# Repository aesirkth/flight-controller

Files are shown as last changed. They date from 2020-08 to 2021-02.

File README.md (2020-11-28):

# Flight Controller <!-- omit in toc -->

This is the embedded software on the Flight Controller for the project Mjollnir. The Flight Controller is on-board the rocket. The Flight Controller communicates with the ground through a radio link during all phases of the flight

The mission objectives for the Mjollnir project relevant to the electronics are the following:

**Primary objectives**

- **E.PO.1** Monitor the rocket while it is on the launchpad and give a “Go”/”No go” signal
- **E.PO.2** Control the rocket while it is on the launchpad
- **E.PO.3** Trigger the drogue parachute’s ejection after apogee
- **E.PO.4** Trigger the main parachute’s ejection before touchdown
- **E.PO.5** Support rocket recovery operations
- **E.PO.6** Record video footage from the rocket

**Secondary objectives**

- **E.SO.1** Send real-time telemetry from the rocket
- **E.SO.2** Receive & display real-time telemetry from the rocket at the Ground Station as long as the rocket is at a reasonable distance
- **E.SO.3** Send real-time video from the rocket
- **E.SO.4** Receive & display real-time video from the rocket at the Ground Station as long as the rocket is at a reasonable distance
- **E.SO.5** Acquire flight data with more sensors than those deemed “mission-critical”
- **E.SO.6** Store all flight data on-board the rocket for further analysis

All of them apply to some extent to the Flight Controller

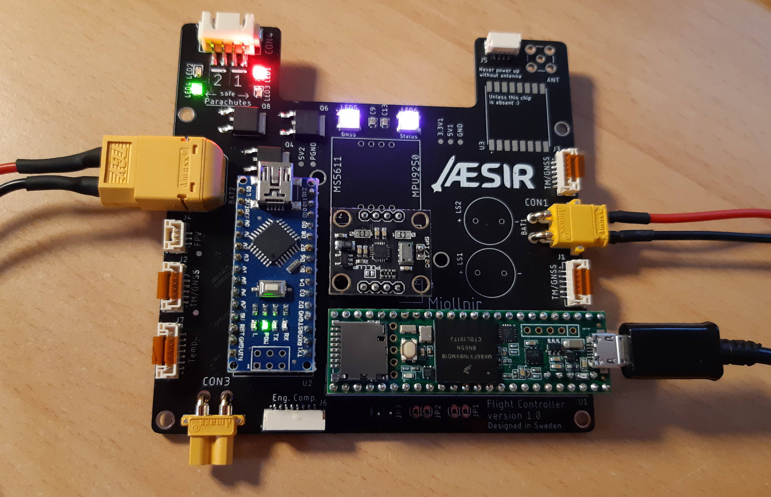
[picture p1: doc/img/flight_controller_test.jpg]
flight_controller_test


# Table of content <!-- omit in toc -->

- [Description](#description)
  - [Hardware](#hardware)
  - [Software](#software)
    - [Installation](#installation)
  - [Tests](#tests)
- [Data protocol](#data-protocol)
- [Folder structure](#folder-structure)

# Description

## Hardware

The Flight Controller is a single PCB with power management, sensors, radio communication, and driver for the actuators used during the flight.

It has the following features:

- Dual microcontroller (main + backup)
- Low power long range LoRa transceiver
- Telemetry output via serial link (x3)
- GNSS support via serial link (x3)
- Compatible with 10 dof breakout board with MS5611 pressure sensors and MPU9250 IMU (2x)
- Compatible with K type thermocouples (2x)
- Flash memory
- EEDs driver for parachute ejection, with ESD protection + visual and audible warning (2x)
- RGB leds to display the board status
- Serial link to FPV transmitter
- CAN Bus

A more detailed description of the hardware is given in [doc/hardware_description.md](doc/hardware_description.md)

## Software

This repository uses [PlatformIO](https://platformio.org/) as the development tool for the two microcontrollers on the Flight Controller.

### Installation

1. Install [PlatformIO Core](https://docs.platformio.org/en/latest/core/index.html) or [PlatformIO IDE](https://platformio.org/install/ide) on your computer
2. Clone this repository
3. [Linux] install [udev](https://docs.platformio.org/en/latest/faq.html?highlight=99#platformio-udev-rules) rules

## Tests

See [test/](test/)

# Data protocol

The protocol to communicate between the Ground Station and the Rocket is detailed in [doc/data_protocol](doc/data_protocol.md)

# Folder structure

```
.
├── doc/
│   ├── img/
│   ├── diagrams/
│   ├── sources
│   |   └── flight_controller_v1.0.pdf
│   ├── data_protocol.md
│   └── hardware_description.md
├── include/
│   ├── hardware_definition_nano.h
│   └── hardware_definition_teensy.h
├── src/                                    // Code folder
│   └── test_companion_teensy.cpp           // Use with hardware_test_teensy
├── test/                                   // Unit tests
│   ├── hardware_test_nano/
│   ├── hardware_test_teensy/
│   └── README.md                           // Documentation for the tests
├── env_nano.ini                            // Extra platformIO config
├── env_teensy.ini                          // Extra platformIO config
├── LICENSE
├── platformio.ini                          // PlatformIO config
└── README.md                               // This file
```

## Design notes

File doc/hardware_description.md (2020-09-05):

# Hardware description <!-- omit in toc -->

*This page describes the version 1.0 of the Flight Controller*

<p align="middle">
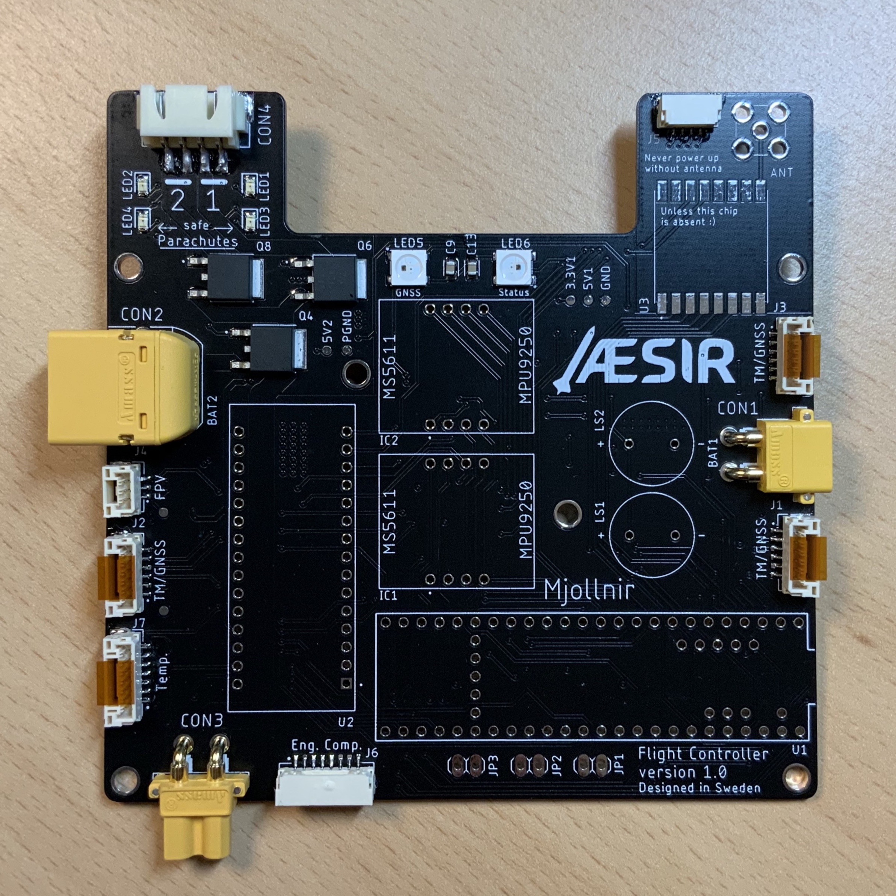
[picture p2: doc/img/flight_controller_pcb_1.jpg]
    
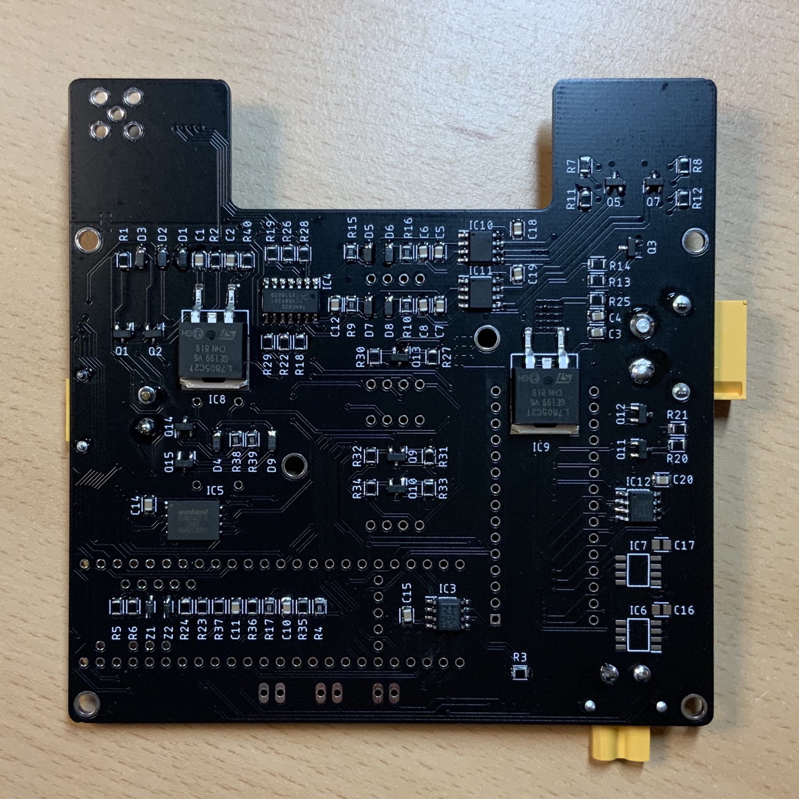
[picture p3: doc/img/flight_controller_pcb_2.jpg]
    
</p>

>Top side and bottom side of the Flight Controller PCB

The schematic of the Flight Controller is here [doc/sources/flight_controller_v1.0.pdf](sources/flight_controller_v1.0.pdf)<br>
The Eagle source files are also available as [doc/sources/flight_controller_v1.0.sch](doc/../sources/flight_controller_v1.0.sch) and [doc/sources/flight_controller_v1.0.brd](doc/../sources/flight_controller_v1.0.brd)

# Table of contents <!-- omit in toc -->

- [Purpose](#purpose)
- [Microcontrollers](#microcontrollers)
- [Power](#power)
  - [Input](#input)
  - [Output](#output)
  - [Turn on the board](#turn-on-the-board)
  - [Power from USB](#power-from-usb)
- [Parachute drivers](#parachute-drivers)
- [Sensors](#sensors)
  - [On the board](#on-the-board)
    - [Air pressure](#air-pressure)
    - [Acceleration & angular velocity](#acceleration--angular-velocity)
  - [Off the board](#off-the-board)
    - [Differential air pressure sensor](#differential-air-pressure-sensor)
    - [Temperature sensors](#temperature-sensors)
- [Radio communication](#radio-communication)
- [GNSS receiver](#gnss-receiver)
- [Flash memory](#flash-memory)
- [Visual and audible signals](#visual-and-audible-signals)
  - [RGB leds](#rgb-leds)
  - [Buzzer](#buzzer)
- [Connectors](#connectors)
  - [Signal](#signal)
    - [Pin numbering](#pin-numbering)
    - [[J1] TM/GNSS](#j1-tmgnss)
    - [[J2] TM/GNSS](#j2-tmgnss)
    - [[J3] TM/GNSS](#j3-tmgnss)
    - [[J4] FPV](#j4-fpv)
    - [[J5] Air pressure sensor](#j5-air-pressure-sensor)
    - [[J6] Engine Computer](#j6-engine-computer)
    - [[J7] External temperature](#j7-external-temperature)
    - [[JP1] Liftoff 1](#jp1-liftoff-1)
    - [[JP2] Liftoff 2](#jp2-liftoff-2)
    - [[JP3] Master Switch](#jp3-master-switch)
  - [Power](#power-1)
    - [[CON1] Battery 1 input](#con1-battery-1-input)
    - [[CON2] Battery 2 input](#con2-battery-2-input)
    - [[CON3] Engine Output](#con3-engine-output)
    - [[CON4] Parachute drivers](#con4-parachute-drivers)
  - [Antenna](#antenna)
    - [[ANT] LoRa antenna](#ant-lora-antenna)

# Purpose

- Validate the overall design of the Flight Controller
- Support the first static fire at the end of the summer 2020
- Support the first tests of the parachute system
- Support the beginning of the code development for the future flight hardware

# Microcontrollers

The Flight Controller has two microcontrollers

| Name | Device | Role | Power |
| --- | --- | --- | ----- |
| Main controller | Teensy 3.6 | Handle the flight data acquisition, parachute ejection, Engine Computer and radio links | BAT1  |
| Backup controller | Arduino Nano | Eject the parachutes in case the main controller fails | BAT2  |

# Power

## Input

Two separate battery inputs are available on the Flight Controller

| Name | Voltage | Role | Connector | Connector type |
| ---- | --- | --- | --- | --- |
| BAT1 | 7.2V | Power the sensors and low power chips | CON1 | XT30, male |
| BAT2 | 11.1V | Power the EEDs for the parachutes, the Engine actuators, and the high power chips | CON2 | XT60, male |

## Output

| Voltage | Role | Connector | Connector type | Current rating |
| --- | --- | --- | --- | --- |
| Same as BAT2 | Power to the Engine | CON3 | XT30, female | Up to 15A |

## Turn on the board

Both batteries are required to use all the fonctions of the Flight Controller

The Flight Controller is ON when the signal `MS_SWITCH` is not tied to `GND` (internal pull-up).
When `MS_SWITCH` is (strongly) pulled down, all the power rails on the board are turned OFF.
The power output on `CON3` is also turned OFF.

`MS_SWITCH` is available on the following connectors :

- J6
- JP3

## Power from USB

Both microcontrollers have an USB input. Caution is required when using power battery power and the USB connection.

**Teensy 3.6**

The Teensy 3.6 board allows to physically isolate the `VIN` rail and the `VUSB` rail by cutting their respective pads apart.

Make sure to isolate `VIN` from `VUSB` on any Teensy used on the Flight Controller to avoid conflicts between the external supply and the usb supply.

<p align="middle">
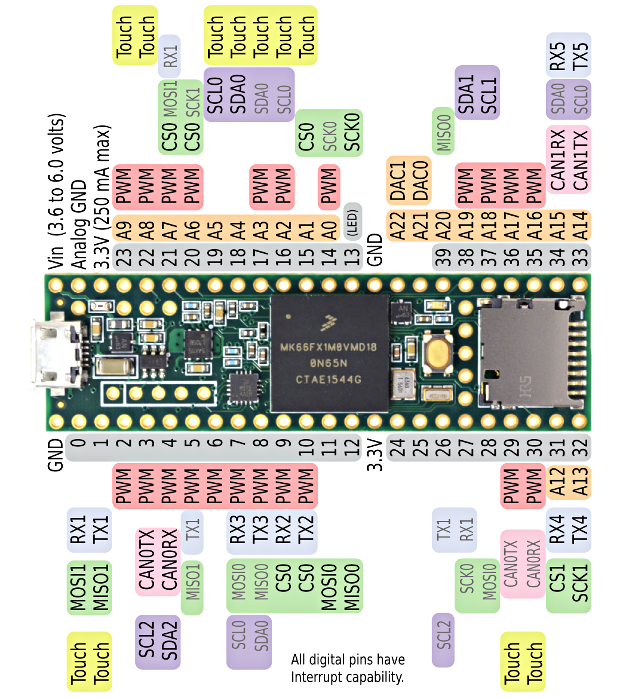
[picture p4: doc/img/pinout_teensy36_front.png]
    
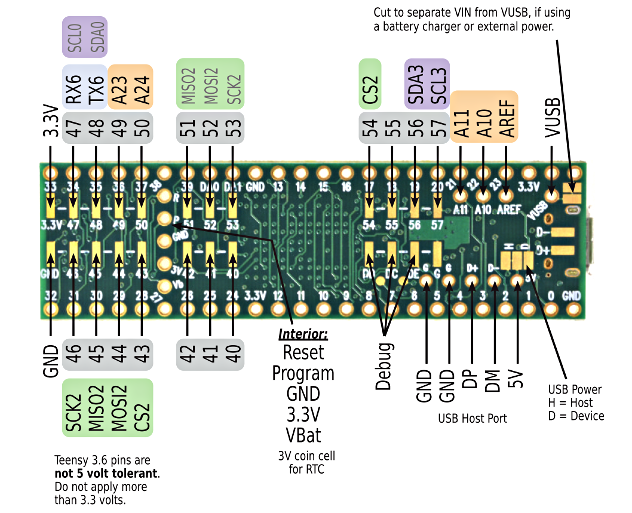
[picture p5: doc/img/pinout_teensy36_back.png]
    
</p>

**Arduino Nano**

The Nano board handles the power supply in a way that allows to use external power and USB power simultaneously. No modification is required.

# Parachute drivers

The Flight Controller can drive two independent parachutes at 12V/5A<br>
The parachutes are ejected from the rocket by Electro Explosive Devices

For safety reasons, both pins of the EEDs must be shorted and grounded when the parachutes are not energized.
This is done with an half H-bridge. The drivers' outputs are either shorted together and with the ground, or one of them is the ground and the other is connected to BAT2. Both the Teensy and the Arduino Nano can trigger the parachutes ejection. A signal from one of them is enough to energize the EED.

A led indicator next to the drivers connector `CON4` shows the state of the two outputs. The code on the Arduino and on the Teensy must activate their respective buzzers before any EED can be energized as a warning signal in case someone were to be close to the EED.

# Sensors

## On the board

### Air pressure

The static air pressure inside the rocket is measured with 2x **MS5611** sensors. The pressure inside the rocket must be equilibrated with the pressure outside the rocket.

A measure of the altitude is derivated from the static pressure

The **MS5611** chips are connected to the SPI bus 0 (`SPI`) of the Teensy.

### Acceleration & angular velocity

The acceleration and angular velocity of the rocket is measured with 2x **MPU9250** sensors. A 3-axis magnetometer is also available on the **MPU9250**.

The measurements from the **MPU9250** are meant to help derive an altitude value and to get the rocket attitude. The performance of the engine can also be recontructed from the acceleration curve during the propulsive phase.

The **MPU9250** are connected to the SPI bus 0 (`SPI`) of the Teensy

## Off the board

### Differential air pressure sensor

Located in the nosecone. ABPDRRT005PG2A5. Used to derive the Mach number

Connected to the I²C bus 0 (`SDA0` & `SCL0`). 5V logic, with level shifter

### Temperature sensors

The board features 2x **MAX31855K** thermocouple-to-digital converters to read the temperature from type_K thermocouples.

The thermocouples will be placed outside the rocket to measure the total air temperature.

The value of the external temperature will be used to derive the air speed during the flight, along with the Mach number

The **MAX31855K** are connected to the SPI bus 0 (`SPI`) of the Teensy

# Radio communication

An **RFM96W** LoRa transceiver at 433 MHz is mounted on the PCB and must always be connected to a 50Ω antenna. It is used as a low power device to receive TC and send the rocket position at low datarates during the flight and after landing.

The **RFM96W** is connected to the SPI bus 1 (`SPI1`) of the Teensy

An **RFD900+** (868MHz) modem can be connected on the **TM/GNSS** connectors of the board

The **RFD900+** is connected on the serial bus corresponding to the number of the connector it is connected to (`Serial1` for J1, `Serial2` for J2, `Serial3` for J3)

# GNSS receiver

A **NEO-M9N** GNSS receiver is used to acquire the rocket position during flight and after landing

The **NEO-M9N** can be used with one of the Serial buses available or over I²C

# Flash memory

A **W25N01GV** flash memory chip (1 Gbit) is available on the Flight Controller to log the flight data

It is connected to the SPI bus 1 (`SPI1`) of the Teensy

# Visual and audible signals

## RGB leds

Two **SK6812** RGB leds are used to display the status of the GNSS signal and the state of the Teensy. The leds are wired in series and are controlled via pin `6` of the Teensy

## Buzzer

The Flight Controller features two CEM-1206S buzzers. One is drived by pin `2` of the Teensy, the other is drived by pin `10` of the Arduino Nano. They work at 2400 Hz.

# Connectors

<p align="middle">
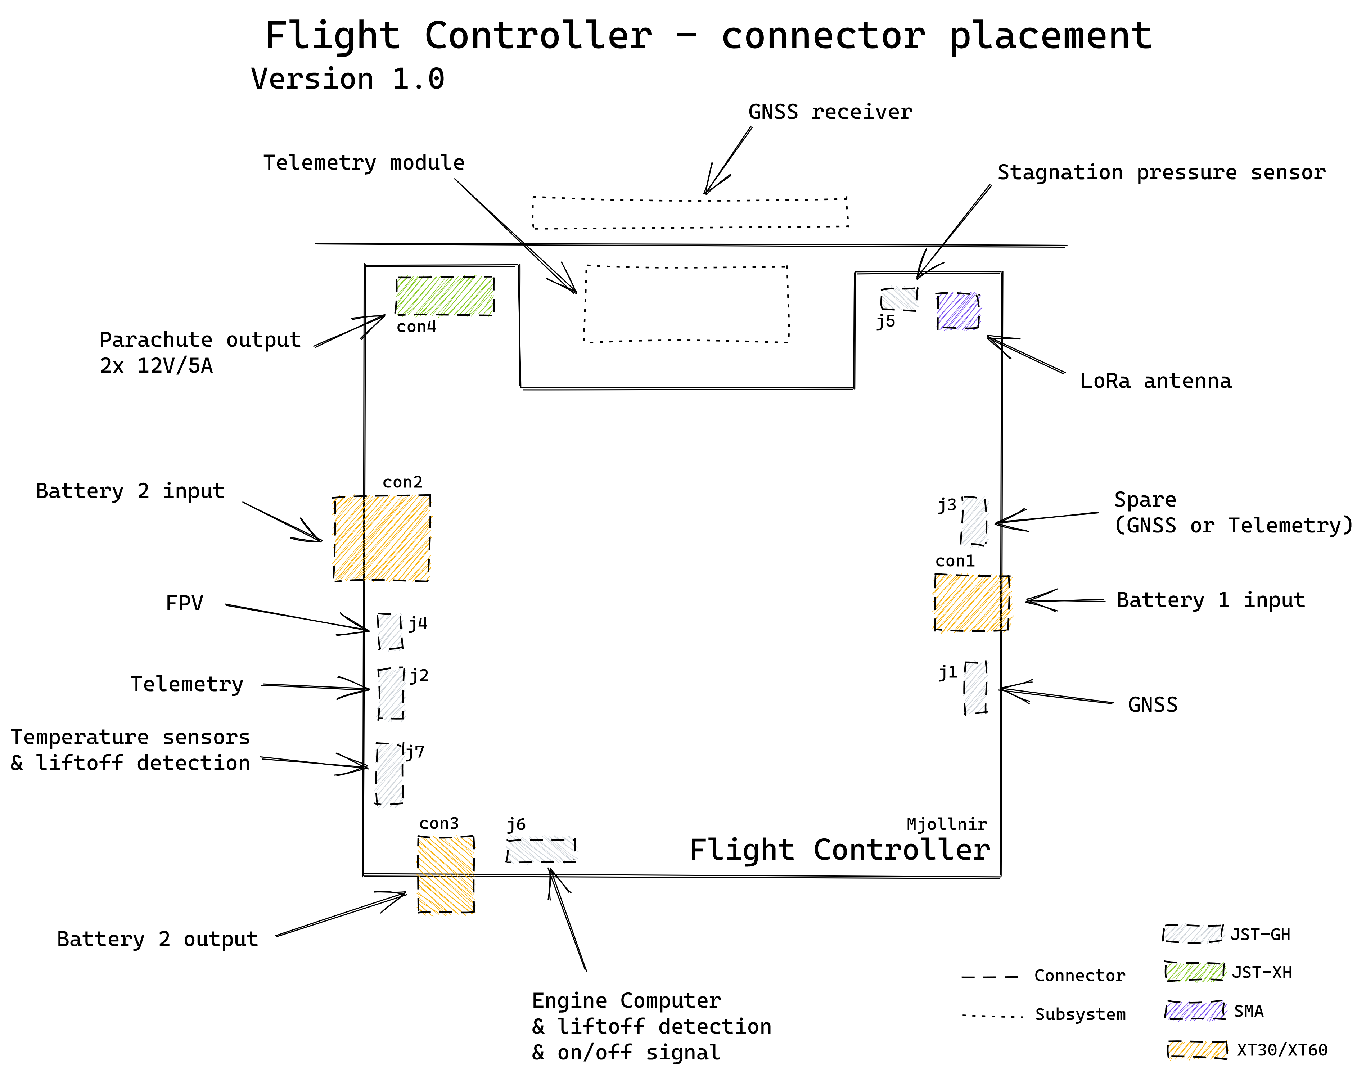
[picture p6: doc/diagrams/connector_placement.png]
    
</p>

## Signal

### Pin numbering

On all JST-GH connectors, pin 1 is the pin with the small triangle marking on the housing. It is also the pin closest to the small dot on the PCB silkscreen.

On all JST-XH connectors, pin 1 is the pin with the small rectangle or triangle marking on the housing.

### [J1] TM/GNSS

JST-GH, 6 pins

Connect a telemetry modem (low power) or a GNSS receiver

| Pin number | 1 | 2 | 3 | 4 | 5 | 6 |
| --- | --- | --- | --- | ---- | ---- | --- |
| Function | 5V1 | RX1 | TX1 | SCL0 | SDA0 | GND |

3.3V logic

### [J2] TM/GNSS

JST-GH, 6 pins

Connect a telemetry modem (high power, up to 1A) or a GNSS receiver<br>
The power on this pin can be turned ON (OFF) by setting pin `35` of the Teensy LOW (HIGH)

| Pin number | 1 | 2 | 3 | 4 | 5 | 6 |
| --- | --- | --- | --- | ---- | ---- | --- |
| Function | 5V2 | RX2 | TX2 | SCL0 | SDA0 | GND |

3.3V logic

### [J3] TM/GNSS

JST-GH, 6 pins

Connect a telemetry modem (low power) or a GNSS receiver

| Pin number | 1 | 2 | 3 | 4 | 5 | 6 |
| --- | --- | --- | --- | ---- | ---- | --- |
| Function | 5V1 | RX3 | TX3 | SCL0 | SDA0 | GND |

3.3V logic

### [J4] FPV

JST-GH, 3 pins

Connect an FPV module (camera + transmitter)<br>
The power on the pin can be turned ON (OFF) by setting pin `36` of the Teensy LOW (HIGH)

| Pin number | 1 | 2 | 3 |
| --- | ---- | --- | --- |
| Function | BAT2 | TX4 | GND |

3.3V logic

### [J5] Air pressure sensor

JST-GH, 4 pins

Connect a differential pressure sensor

| Pin number | 1 | 2 | 3 | 4 |
| --- | --- | ---- | ---- | --- |
| Function | 5V1 | SCL0 | SDA0 | GND |

5V logic

### [J6] Engine Computer

JST-GH, 8 pins

Connector to the Engine Computer<br>
Can provide 200 mA<br>
Also contains `MS_SWITCH` and `LIFTOFF_2` signals to the bottom of the rocket

| Pin number | 1 | 2 | 3 | 4 | 5 | 6 | 7 | 8 |
| --- | --- | --- | ----- | ----- | --- | --- | --- | --- |
| Function | 5V1 | GND | CANH0 | CANL0 | MS_SWITCH | GND | LIFTOFF_2 | GND |

3.3V logic

### [J7] External temperature

JST-GH, 7 pins

Two type-K thermocouples and `LIFTOFF_1` signal

| Pin number | 1 | 2 | 3 | 4 | 5 | 6 | 7 |
| --- | --- | --- | --- | --- | --- | --- | --- |
| Function | NC  | T1- | T1+ | T2- | T2+ | LIFTOFF_1 | GND |

3.3V logic

### [JP1] Liftoff 1

2.54 mm male pin header

Easy access to the `LIFTOFF_1` signal

| Pin | left | right |
| --- | --- | ----- |
| Function | LIFTOFF_1 | GND |

### [JP2] Liftoff 2

2.54 mm male pin header

Easy access to the `LIFTOFF_2` signal

| Pin | left | right |
| --- | --- | ----- |
| Function | LIFTOFF_2 | GND |

### [JP3] Master Switch

2.54 mm male pin header

Easy access to the `MS_SWITCH` signal

| Pin | left | right |
| --- | --- | ----- |
| Function | MS_SWITCH | GND |

## Power

### [CON1] Battery 1 input

XT-30, male

2S LiPo battery

### [CON2] Battery 2 input

XT-60, male

3S LiPo battery

### [CON3] Engine Output

XT-30, female

Power output to the Engine actuators<br>
From BAT2, max 15A

### [CON4] Parachute drivers

JST-XH, 4 pins

Outputs to the parachutes' EEDs<br>
Rated 12V/3A, can deliver 5A for short periods

| Pin number | 1 | 2 | 3 | 4 |
| --- | --- | --- | --- | --- |
| Function | GND | PARACHUTE_1 | GND | PARACHUTE_1 |

## Antenna

### [ANT] LoRa antenna

50Ω SMA connector

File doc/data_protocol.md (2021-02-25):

# Data Protocol <!-- omit in toc -->

Here is a description of the data protocol between the Rocket and the Ground Station for the Mjollnir project.

This protocol defines how Telecommands and Telemetry are transmitted between the Ground Station, the Engine Computer, and the Flight Controller.

The following repositories follow this data protocol:

- [aesirkth/flight-controller](https://github.com/aesirkth/flight-controller)
- [aesirkth/ground-control](https://github.com/aesirkth/ground-control)
- *engine computer repository*

The diagrams in this document can be edited using the online tool [diagrams.net](https://www.diagrams.net/). Just import the `.xml` files. Export the diagrams to `.png` and to `.xml` (compressed) and save them back here after modification.

The HTML tables in this document can be edited using the online tool [tablesgenerator.com](https://www.tablesgenerator.com/html_tables). Simply click "File / Paste table data" and paste the table. Make sure to check "Do not generate CSS" and uncheck "Compact mode".

# Table of contents <!-- omit in toc -->

- [Overview](#overview)
- [Development plan](#development-plan)
  - [Static Fire](#static-fire)
  - [Launch](#launch)
- [Serial links](#serial-links)
- [CAN Bus](#can-bus)
- [Data protocol](#data-protocol)
  - [Telecommand](#telecommand)
    - [Communication sequence](#communication-sequence)
    - [Commands description](#commands-description)
      - [Engine Controller](#engine-controller)
      - [Flight Controller](#flight-controller)
  - [Telemetry](#telemetry)
    - [Communication sequence](#communication-sequence-1)
    - [Data description](#data-description)
      - [Engine Controller](#engine-controller-1)
      - [Flight Controller](#flight-controller-1)
      - [About time stamps](#about-time-stamps)
      - [About lost frames](#about-lost-frames)

# Overview

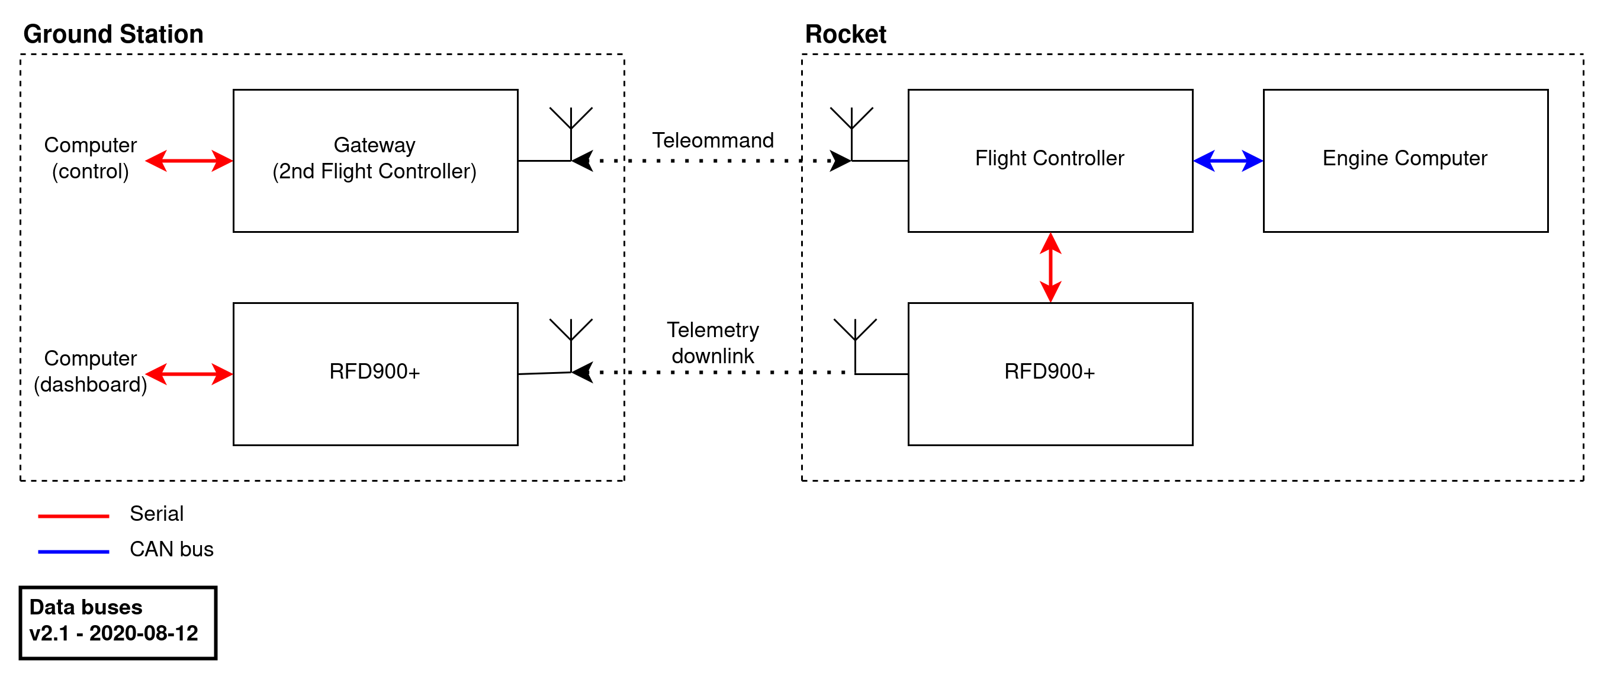
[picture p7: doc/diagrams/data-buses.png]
buses

>Overview of the data buses between the Ground Station and the Rocket<br>
The source file can be found in [doc/diagrams/data-buses.xml](diagrams/data-buses.xml) and edited using [diagrams.net](https://www.diagrams.net/) \[[desktop](https://github.com/jgraph/drawio-desktop/releases)]

The Gateway is connected to the Control computer through the USB connector of the Flight Controller<br>
The RFD900+ on the Ground Station side is connected to the Dashboard computer through an FTDI USB cable.

The Flight Controller on the Ground Station 'Gateway' is a preliminary solution to have the Control computer talk to the Rocket's Flight Controller during the first static fire.

# Development plan

The work on this data protocol is still preliminary. The development will be iterative and the first milestone is the static fire planned for the end of the beginning of 2021. The protocol will be refined later on to better allocate the telemetry sent back to the Ground Station.

## Static Fire

Drivers:

- Send commands to the Rocket and have the relevant ones forwarded to the Engine Computer
- Send back Telemetry to the Ground Station, mainly comprised of measurement samples from the Engine Computer
- No logic on the Flight Controller for the Telemetry packets, the packets are simply forwarded to the Ground Station. We will try to store the telemetry on the FC memory as well, so we can have data with higher sampling rates even if it is offline, as well as a backup.

## Launch

Drivers:

- Maximize the amount of data downlinked from the Rocket, by optimizing how the data packets are processed by the Flight Controller and maybe also the Ground Station.
- Be more resilient to loss of frames.

# Serial links

All serial links share the same configuration. The baud rate is `57600` (might need to be changed to 115200). The airspeed between the RFD900+ modems is 64kbps.

A frame on the serial links looks like this:

| Byte number | Description |
| --- | --- |
| 0 | Frame separator: `0x0A` |
| 1 | Frame separator: `0x0D` |
| 2 | Frame ID |
| 3 | Data byte 0 |
| 4 | Data byte 1 |
| [...] | [...] |
| N+3 | Data byte N |

The length of the data field is variable

# CAN Bus

> **Note:** the CAN bus between the Engine Computer and the Flight Controller can be extended to additional boards in future developments.

CAN bus: CAN2.0 (FlexCAN) @1Mbit/s with termination 120Ω resistors on the Flight Controller side and on the Engine Computer side.

Base frame format (11 identifier bits)

>**Note:** The Time Sync of the Engine Computer will be handled by the Flight Controller. The EC will send a request package and the FC will answer it using its currently configured system time (this can be the time set by the Ground Station or the time received through GNSS). 

# Data protocol

The term `ID` is used below to denote `identifier field` of the CAN Bus and byte 2 (`Frame ID`) of a frame over the serial links.

The `identifier field` is an 11 bits field but only the 8 lower bits are used to make the data on the CAN Bus as similar as possible to the data on the serial buses. The remaining `ID` values `100` - `7FF` are available for data transfer between on-board systems over the CAN Bus only, and cannot be sent to ground.

Each message on the Telecommand TC link and the Telemetry TM link has a unique ID.

<table>
<thead>
  <tr>
    <th>ID</th>
    <th>Frame Type</th>
    <th>From</th>
    <th>To</th>
    <th>Unique IDs</th>
  </tr>
</thead>
<tbody>
  <tr>
    <td>0x00 - 0x0F</td>
    <td>TC</td>
    <td>Ground Station</td>
    <td>Flight Controller</td>
    <td>16</td>
  </tr>
  <tr>
    <td>0x10 - 0x1F</td>
    <td>TC</td>
    <td>Flight Controller</td>
    <td>Ground Station</td>
    <td>16</td>
  </tr>
  <tr>
    <td>0x20 - 0x2F</td>
    <td>TC</td>
    <td>Ground Station</td>
    <td>Engine Computer</td>
    <td>16</td>
  </tr>
  <tr>
    <td>0x30 - 0x3F</td>
    <td>TC</td>
    <td>Engine Computer</td>
    <td>Ground Station</td>
    <td>16</td>
  </tr>
  <tr>
    <td>0x40 - 0x7F</td>
    <td>TM</td>
    <td>Flight Controller</td>
    <td>Ground Station</td>
    <td>64</td>
  </tr>
  <tr>
    <td>0x80 - 0xFF</td>
    <td>TM</td>
    <td>Engine Computer</td>
    <td>Ground Station</td>
    <td>128</td>
  </tr>
  </tr>
</tbody>
</table>

## Telecommand

The Telecommand link is a low data rate radio link over LoRa at 433 MHz. The communication will work on a request-response basis where the Ground Station sends a command and the Flight Controller or Engine Computer replies back, but at the same time some data will be streamed from the FC at a low rate.

### Communication sequence

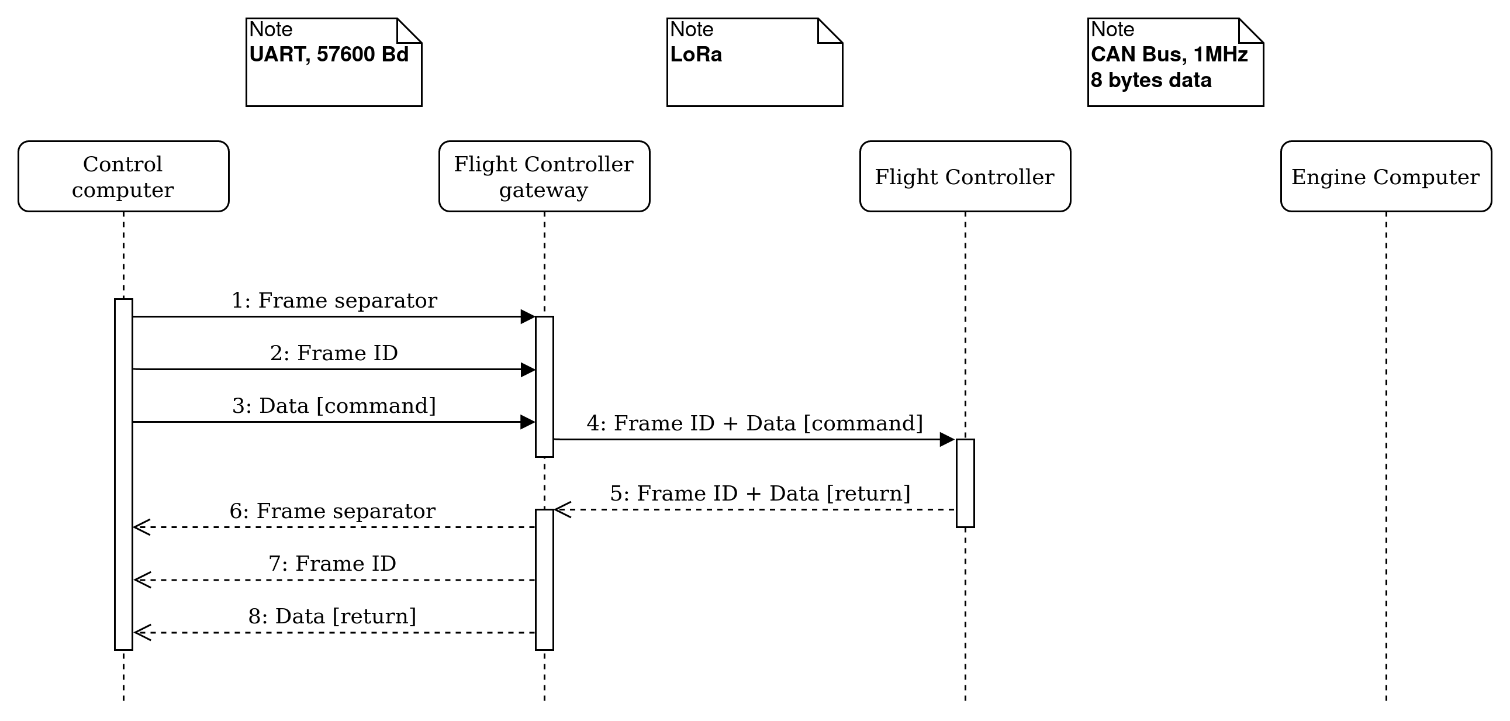
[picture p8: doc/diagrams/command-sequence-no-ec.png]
commands-sequence-no-ec

>Command sequence to the Rocket. Command addressed to the Flight Controller<br>
The source file can be found in [doc/diagrams/command-sequence.xml](diagrams/command-sequence.xml) and edited using [diagrams.net](https://www.diagrams.net/) \[[desktop](https://github.com/jgraph/drawio-desktop/releases)]

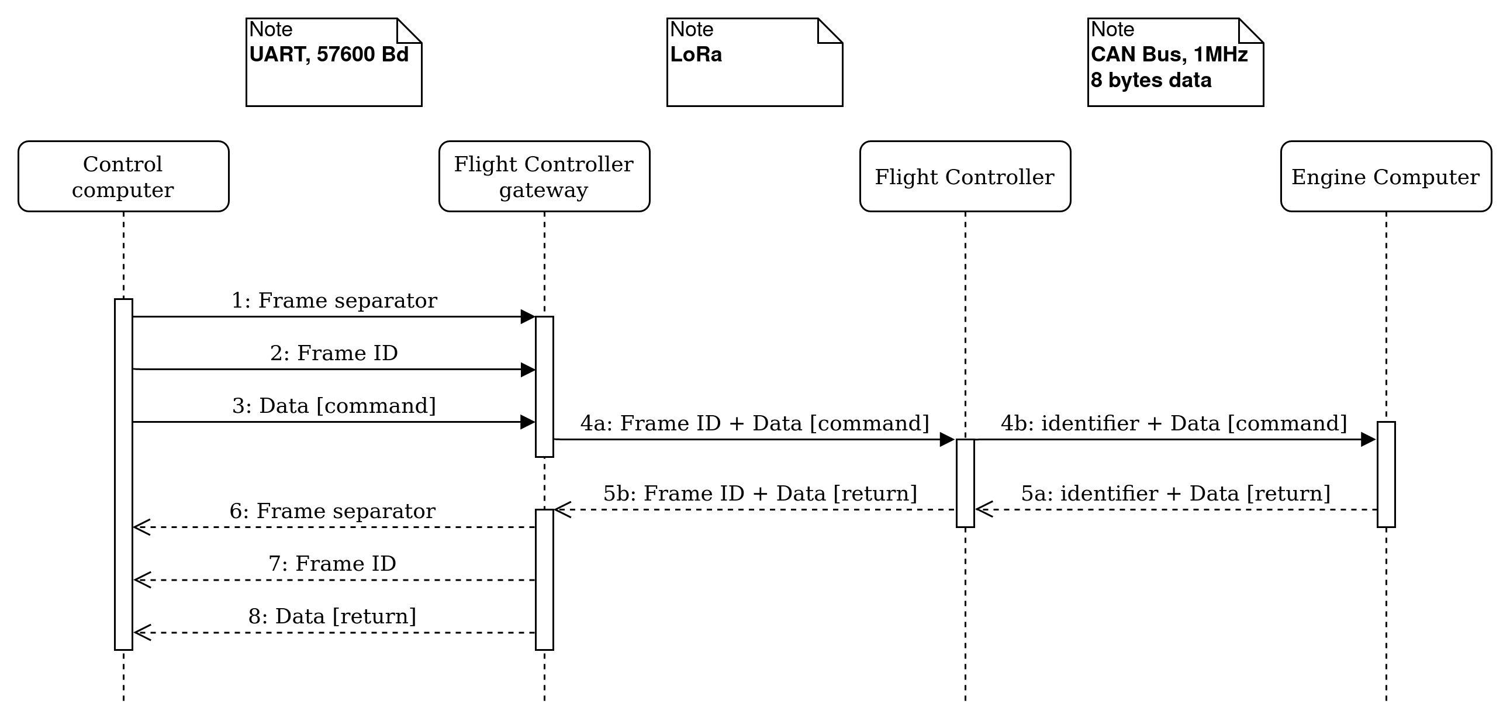
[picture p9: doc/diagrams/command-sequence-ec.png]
commands-sequence-no-ec

>Command sequence to the Rocket. Command addressed to the Engine Controller<br>
The source file can be found in [doc/diagrams/command-sequence.xml](diagrams/command-sequence.xml) and edited using [diagrams.net](https://www.diagrams.net/) \[[desktop](https://github.com/jgraph/drawio-desktop/releases)]

### Commands description

ALL DATA MUST BE LITTLE-ENDIAN

#### Flight Controller

Commands sent from the Ground Station to the Flight Controller
<table>
<thead>
  <tr>
    <th>ID</th>
    <th>Description</th>
    <th>Data size</th>
    <th>Data</th>
    <th>Comment</th>
    <th>Rate</th>
  </tr>
</thead>
<tbody>
  <tr>
    <td>0x00</td>
    <td>Time Sync</td>
    <td>4</td>
    <td>system_time</td>
    <td>uint32_t, hhmmss.sss</td>
    <td> </td>
  </tr>
  <tr>
    <td>0x01</td>
    <td>Set Power Mode</td>
    <td>1</td>
    <td>TBD</td>
    <td> </td>
    <td> </td>
  </tr>
  <tr>
    <td>0x02</td>
    <td>Set Radio Equipment</td>
    <td>1</td>
    <td>bit0: is_fpv_en<br>bit1: is_tm_en</td>
    <td>Default state is 0</td>
    <td> </td>
  </tr>
  <tr>
    <td>0x03</td>
    <td>Set Parachute Output</td>
    <td>1</td>
    <td>bit0: is_parachute_armed<br>bit1: is_parachute1_en<br>bit2: is_parachute2_en</td>
    <td>Default state is 0 <br>Must set is_armed to 1 before<br>a parachute can be enabled</td>
    <td> </td>
  </tr>
  <tr>
    <td>0x04</td>
    <td>Set Data Logging</td>
    <td>1</td>
    <td>bit0: is_logging_en</td>
    <td>enables data logging to SD-card and/or flash-chip</td>
    <td> </td>
  </tr>
  <tr>
    <td>0x05</td>
    <td>Dump flash chip</td>
    <td>1</td>
    <td>bit0: dump_sd <br>bit1: dump_usb</td>
    <td></td>
    <td> </td>
  </tr>
</tbody>
</table>

Replies sent from the Flight Controller to the Ground Station and stremed data
<table>
<thead>
  <tr>
    <th>ID</th>
    <th>Description</th>
    <th>Data size</th>
    <th>Data</th>
    <th>Comment</th>
    <th>Rate</th>
  </tr>
</thead>
<tbody>
  <tr>
    <td>0x10</td>
    <td>Return Time Sync</td>
    <td>N/A</td>
    <td> </td>
    <td> </td>
    <td> </td>
  </tr>
  <tr>
    <td>0x11</td>
    <td>Return Power Mode</td>
    <td>1</td>
    <td>TBD</td>
    <td> </td>
    <td> </td>
  </tr>
  <tr>
    <td>0x12</td>
    <td>Return Radio Equipment</td>
    <td>1</td>
    <td>bit0: is_fpv_en<br>bit1: is_tm_en</td>
    <td> </td>
    <td> </td>
  </tr>
  <tr>
    <td>0x13</td>
    <td>Return Parachute Output</td>
    <td>1</td>
    <td>bit0: is_parachute_armed<br>bit1: is_parachute1_en<br>bit2: is_parachute2_en</td>
    <td> </td>
    <td> </td>
  </tr>
  <tr>
    <td rowspan="2">0x14</td>
    <td rowspan="2">Onboard Battery Voltage</td>
    <td rowspan="2">4</td>
    <td>battery_1</td>
    <td>uint16_t, in 0.01V</td>
    <td rowspan="2">0.2</td>
  </tr>
  <tr>
    <td>battery_2</td>
    <td>uint16_t, in 0.01V</td>
  </tr>
  <tr>
    <td rowspan="4">0x15</td>
    <td rowspan="4">GNSS data</td>
    <td rowspan="4">14</td>
    <td>gnss_time</td>
    <td>uint32_t, in hhmmss.sss</td>
    <td rowspan="4">0.2</td>
  </tr>
  <tr>
    <td>latitude</td>
    <td>int32_t, in ddmm.mmmm</td>
  </tr>
  <tr>
    <td>longitude</td>
    <td>int32_t, in dddmm.mmmm</td>
  </tr>
  <tr>
    <td>h_dop</td>
    <td>uint16_t, in 0.01</td>
  </tr>
  <tr>
    <td rowspan="3">0x16</td>
    <td rowspan="3">Flight Controller Status</td>
    <td rowspan="3">3</td>
    <td>HW_state</td>
    <td>uint8_t</td>
    <td rowspan="3">0.2</td>
  </tr>
  <tr>
    <td>SW_state</td>
    <td>uint8_t</td>
  </tr>
  <tr>
    <td>mision_state</td>
    <td>uint8_t, enum</td>
  </tr>
  <tr>
    <td>0x17</td>
    <td>Return Data Logging</td>
    <td>1</td>
    <td>bit0: is_logging_en</td>
    <td> </td>
    <td> </td>
  </tr>
  <tr>
    <td>0x18</td>
    <td>Return dump flash</td>
    <td>1</td>
    <td>bit0: dump_sd <br>bit1: dump_usb</td>
    <td> </td>
    <td> </td>
  </tr>
  <tr>
    <td>0x19</td>
    <td>Return Handshake</td>
    <td>0</td>
    <td></td>
    <td> </td>
    <td> </td>
  </tr>
</tbody>
</table>

## Telemetry

The Telemetry link is a high data rate radio link over FHSS at 868 MHz. It is technically bi-directional but only the downlink capability is used.

### Communication sequence

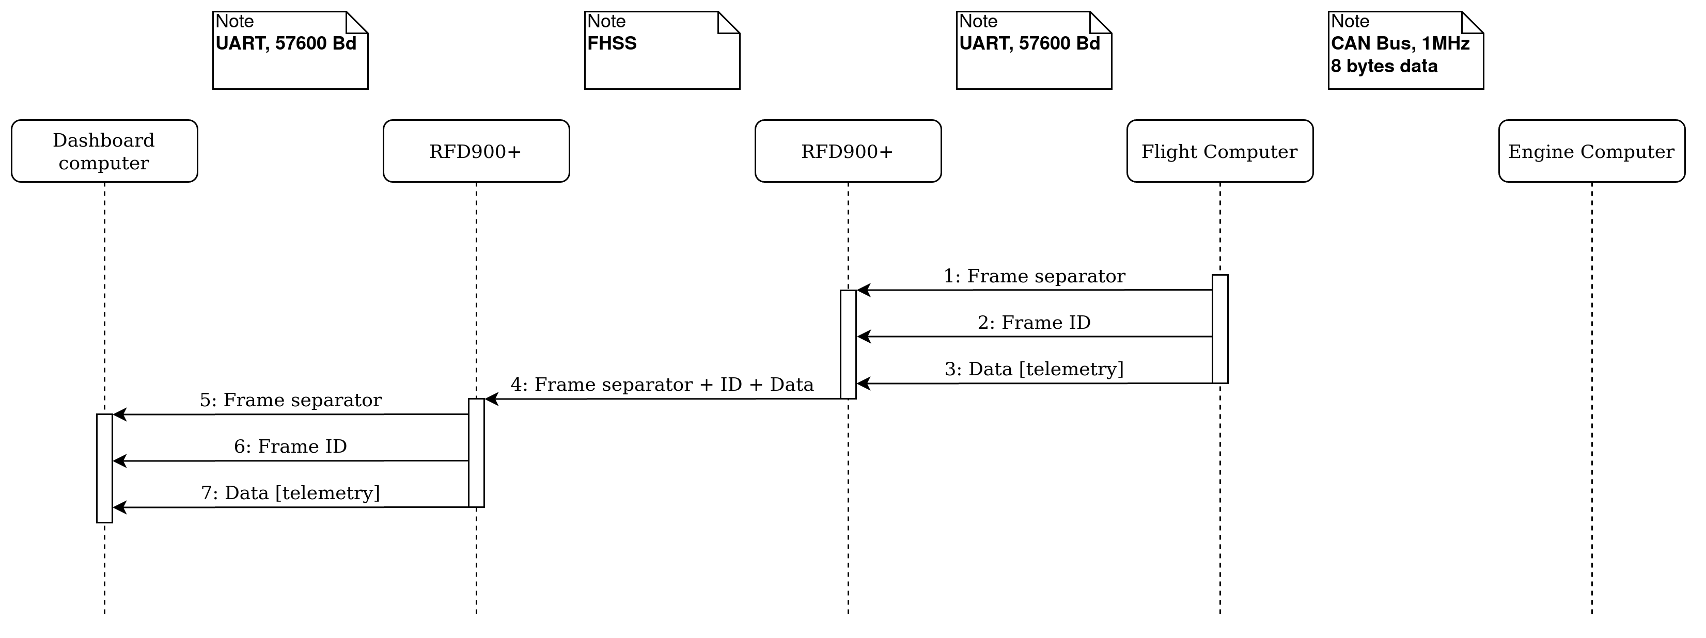
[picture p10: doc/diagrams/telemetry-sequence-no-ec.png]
telemetry-sequence-no-ec

>Telemetry sequence from the Rocket. Telemetry from the Flight Controller<br>
The source file can be found in [doc/diagrams/telemetry-sequence.xml](diagrams/telemetry-sequence.xml) and edited using [diagrams.net](https://www.diagrams.net/) \[[desktop](https://github.com/jgraph/drawio-desktop/releases)]

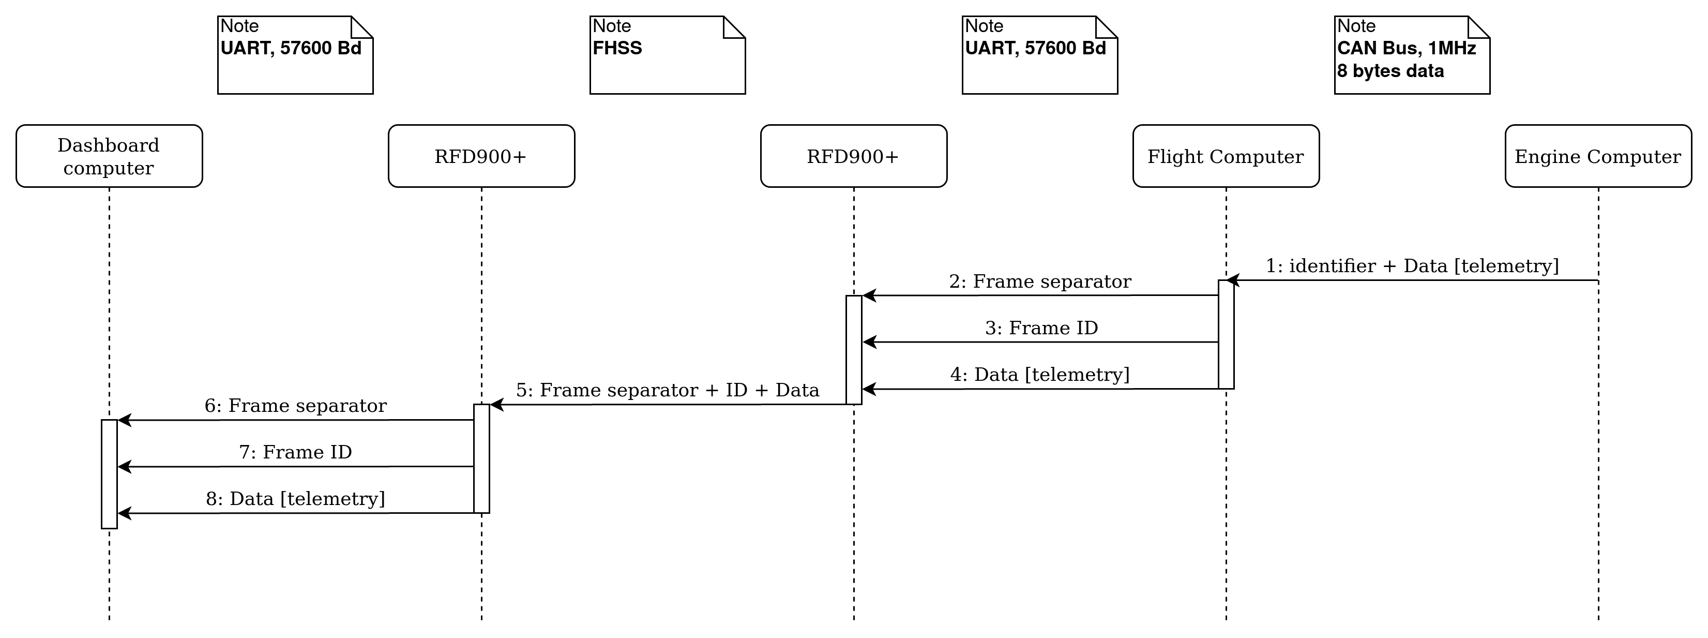
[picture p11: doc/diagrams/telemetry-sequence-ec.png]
telemetry-sequence-no-ec

>Telemetry sequence from the Rocket. Telemetry from the Engine Controller<br>
The source file can be found in [doc/diagrams/telemetry-sequence.xml](diagrams/telemetry-sequence.xml) and edited using [diagrams.net](https://www.diagrams.net/) \[[desktop](https://github.com/jgraph/drawio-desktop/releases)]

### Data description

ALL DATA MUST BE LITTLE-ENDIAN

#### Flight Controller

<table>
<thead>
  <tr>
    <th>ID</th>
    <th>Description</th>
    <th>Data size</th>
    <th>Data</th>
    <th>Comment</th>
    <th>Tx Rate</th>
    <th>Sampling Rate</th>
  </tr>
</thead>
<tbody>
  <tr>
    <td>0x40</td>
    <td>Time since boot - millis</td>
    <td>4</td>
    <td>ms_since_boot</td>
    <td>uint32_t</td>
    <td> </td>
    <td></td>
  </tr>
  <tr>
    <td>0x41</td>
    <td>Time since boot - micros</td>
    <td>8</td>
    <td>us_since_boot</td>
    <td>uint64_t</td>
    <td> </td>
    <td></td>
  </tr>
  <tr>
    <td>0x42</td>
    <td>Current time</td>
    <td>4 </td>
    <td>current_time</td>
    <td>uint32_t, in hhmmss.sss<br>interpolated from gps time</td>
    <td></td>
    <td></td>
  </tr>
  <tr>
    <td rowspan="3">0x43</td>
    <td rowspan="3">GNSS Data 1</td>
    <td rowspan="3">12</td>
    <td>gnss_time</td>
    <td>uint32_t, in hhmmss.sss</td>
    <td rowspan="3">2</td>
    <td rowspan="3">2</td>
  </tr>
  <tr>
    <td>latitude</td>
    <td>int32_t, in ddmm.mmmm</td>
  </tr>
  <tr>
    <td>longitude</td>
    <td>int32_t, in dddmm.mmmm</td>
  </tr>
  <tr>
    <td rowspan="6">0x44</td>
    <td rowspan="6">GNSS Data 2</td>
    <td rowspan="6">12</td>
    <td>altitude</td>
    <td>int32_t, in 0.1 meters</td>
    <td rowspan="6">2</td>
    <td rowspan="6">2</td>
  </tr>
  <tr>
    <td>heading</td>
    <td>int16_t, in degrees</td>
  </tr>
  <tr>
    <td>horiz_speed</td>
    <td>int16_t, in 0.1 km/h</td>
  </tr>
  <tr>
    <td>fix_status</td>
    <td>uint8_t, {0 = No Fix, 1 = 2D, 2 = 3D}</td>
  </tr>
  <tr>
    <td>n_satellites</td>
    <td>uint8_t</td>
  </tr>
  <tr>
    <td>h_dop</td>
    <td>uint16_t, in 0.1</td>
  </tr>
  <tr>
    <td rowspan="2">0x45</td>
    <td rowspan="2">Inside Static Temperature</td>
    <td rowspan="2">8</td>
    <td>temperature_1</td>
    <td>int32_t, in 0.01 ºC</td>
    <td rowspan="2">2</td>
    <td rowspan="2">TBD</td>
  </tr>
  <tr>
    <td>temperature_2</td>
    <td>int32_t, in 0.01 ºC</td>
  </tr>
  <tr>
    <td rowspan="2">0x46</td>
    <td rowspan="2">Inside Static Pressure</td>
    <td rowspan="2">8</td>
    <td>pressure_1</td>
    <td>int32_t, in 0.01 mbar</td>
    <td rowspan="2">20</td>
    <td rowspan="2">TBD</td>
  </tr>
  <tr>
    <td>pressure_2</td>
    <td>int32_t, in 0.01 mbar</td>
  </tr>
  <tr>
    <td rowspan="9">0x47</td>
    <td rowspan="9">IMU 1</td>
    <td rowspan="9">18</td>
    <td>accel_x</td>
    <td>int16_t</td>
    <td rowspan="9">20</td>
    <td rowspan="9">TBD</td>
  </tr>
  <tr>
    <td>accel_y</td>
    <td>int16_t</td>
  </tr>
  <tr>
    <td>accel_z</td>
    <td>int16_t</td>
  </tr>
  <tr>
    <td>gyro_x</td>
    <td>int16_t</td>
  </tr>
  <tr>
    <td>gyro_y</td>
    <td>int16_t</td>
  </tr>
  <tr>
    <td>gyro_z</td>
    <td>int16_t</td>
  </tr>
  <tr>
    <td>magnet_x</td>
    <td>int16_t</td>
  </tr>
  <tr>
    <td>magnet_y</td>
    <td>int16_t</td>
  </tr>
  <tr>
    <td>magnet_z</td>
    <td>int16_t</td>
  </tr>
  <tr>
    <td rowspan="9">0x48</td>
    <td rowspan="9">IMU 2</td>
    <td rowspan="9">18</td>
    <td>accel_x</td>
    <td>int16_t</td>
    <td rowspan="9">20</td>
    <td rowspan="9">TBD</td>
  </tr>
  <tr>
    <td>accel_y</td>
    <td>int16_t</td>
  </tr>
  <tr>
    <td>accel_z</td>
    <td>int16_t</td>
  </tr>
  <tr>
    <td>gyro_x</td>
    <td>int16_t</td>
  </tr>
  <tr>
    <td>gyro_y</td>
    <td>int16_t</td>
  </tr>
  <tr>
    <td>gyro_z</td>
    <td>int16_t</td>
  </tr>
  <tr>
    <td>magnet_x</td>
    <td>int16_t</td>
  </tr>
  <tr>
    <td>magnet_y</td>
    <td>int16_t</td>
  </tr>
  <tr>
    <td>magnet_z</td>
    <td>int16_t</td>
  </tr>
  <tr>
    <td rowspan="2">0x49</td>
    <td rowspan="2">External Temperature</td>
    <td rowspan="2">4</td>
    <td>temp_1</td>
    <td>int16_t</td>
    <td rowspan="2">10</td>
    <td rowspan="2">TBD</td>
  </tr>
  <tr>
    <td>temp_2</td>
    <td>int16_t</td>
  </tr>
  <tr>
    <td rowspan="2">0x4A</td>
    <td rowspan="2">Air Speed</td>
    <td rowspan="2">4</td>
    <td>pitot</td>
    <td>int16_t</td>
    <td rowspan="2">20</td>
    <td rowspan="2">TBD</td>
  </tr>
  <tr>
    <td>calculated</td>
    <td>int16_t</td>
  </tr>
  <tr>
    <td rowspan="2">0x4B</td>
    <td rowspan="2">Onboard Battery Voltage</td>
    <td rowspan="2">4</td>
    <td>battery_1</td>
    <td>uint16_t, in 0.01V</td>
    <td rowspan="2">2</td>
    <td rowspan="2">10</td>
  </tr>
  <tr>
    <td>battery_2</td>
    <td>uint16_t, in 0.01V</td>
  </tr>
  <tr>
    <td rowspan="3">0x4C</td>
    <td rowspan="3">Flight Controller Status</td>
    <td rowspan="3">3</td>
    <td>HW_state</td>
    <td>uint8_t<br>bit0: is_parachute_armed<br>bit1: is_parachute_1_en<br>bit2: is_parachute_2_en<br>bit3: is_fpv_en<br>bit4: is_telemetry_en</td>
    <td rowspan="3">10</td>
    <td rowspan="3">10</td>
  </tr>
  <tr>
    <td>SW_state</td>
    <td>uint8_t</td>
  </tr>
  <tr>
    <td>mision_state</td>
    <td>uint8_t, enum</td>
  </tr>
</tbody>
</table>

#### About time stamps

The data acquisition process is the following:

1. Save all acquired data to a buffer
1. Sync the internal clock to GPS time and interpolate it
1. At a regular interval send the current time and the stored buffer
1. Every few seconds record the delays in the CAN-system
1. If needed use the delays to reconstruct the actual time on the ground station

This allows to reduce the overhead on the Telemetry link by only sending one time stamp for all the data acquired in one loop.
The error in acquisition time is acceptable as the sampling loop is assumed to be short with respect to the measured phenomena.
All the sensors may not be sampled in every loop or may be sampled without sending the samples to the ground. The sensors that require low sampling rates can simply be sampled and sent every **X** loop

#### About lost frames

Some cases might exist where the time frame is not received on the Ground Station.

On Sigmundr launch (2019), the telemetry frames were ~100 bytes long. It was noticed that when a failure occured, the whole frame was lost instead of just small bits at the beginning or so. **This has to do with how the RFD900+ modems handle the data transmission and should be further investigated.**

Possible mitigations for early uses of this protocol can be:

- Time stamp all packets at reception time and compare this time with the time frame.
- Assume no packet loss. (realistic at close range, < 1km with line of sight)
- Group the frames in a big packet (wait and send all at once) like was done on Sigmundr and hope for a pass / fail for one hole sampling loop.

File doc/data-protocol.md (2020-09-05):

# Data Protocol <!-- omit in toc -->

Here is a description of the data protocol between the Rocket and the Ground Station for the Mjollnir project

This protocol defines how Telecommands and Telemetry are transmitted between the Ground Station, the Engine Computer, and the Flight Controller

The following repositories follow this data protocol:

- [aesirkth/flight-controller](https://github.com/aesirkth/flight-controller)
- [aesirkth/ground-control](https://github.com/aesirkth/ground-control)
- *engine computer repository*

The diagrams in this document can be edited using the online tool [diagrams.net](https://www.diagrams.net/). Just import the `.xml` files. Export the diagrams to `.png` and to `.xml` (compressed) and save them back here after modification

The HTML tables in this document can be edited using the online tool [tablesgenerator.com](https://www.tablesgenerator.com/html_tables). Simply click "File / Paste table data" and paste the table. Make sure to check "Do not generate CSS" and uncheck "Compact mode"

# Table of contents <!-- omit in toc -->

- [Overview](#overview)
- [Development plan](#development-plan)
  - [Static Fire](#static-fire)
  - [Launch](#launch)
- [Serial links](#serial-links)
- [CAN Bus](#can-bus)
- [Data protocol](#data-protocol)
  - [Telecommand](#telecommand)
    - [Communication sequence](#communication-sequence)
    - [Commands description](#commands-description)
      - [Engine Controller](#engine-controller)
      - [Flight Controller](#flight-controller)
  - [Telemetry](#telemetry)
    - [Communication sequence](#communication-sequence-1)
    - [Data description](#data-description)
      - [Engine Controller](#engine-controller-1)
      - [Flight Controller](#flight-controller-1)
      - [About time stamps](#about-time-stamps)
      - [About lost frames](#about-lost-frames)

# Overview

buses
>Overview of the data buses between the Ground Station and the Rocket<br>
The source file can be found in [doc/diagrams/data-buses.xml](diagrams/data-buses.xml) and edited using [diagrams.net](https://www.diagrams.net/) \[[desktop](https://github.com/jgraph/drawio-desktop/releases)]

The Gateway is connected to the Control computer through the USB connector of the Flight Controller<br>
The RFD900+ on the Ground Station side is connected to the Dashboard computer through an FTDI USB cable

The Flight Controller on the Ground Station 'Gateway' is a preliminary solution to have the Control computer talk to the Rocket's Flight Controller during the first static fire

# Development plan

The work on this data protocol is still preliminary. The development will be iterative and the first milestone is the static fire planned for the end of the summer 2020. The protocol will be refined later on to better allocate the telemetry sent back to the Ground Station.

## Static Fire

Drivers:

- Send commands to the Rocket and have the relevant ones forwarded to the Engine Computer
- Send back Telemetry to the Ground Station, mainly comprised of measurement samples from the Engine Computer
- No logic on the Flight Controller for the Telemetry packets, the packets are simply forwarded to the Ground Station

## Launch

Drivers:

- Maximize the amount of data downlinked from the Rocket, by optimizing how the data packets are processed by the Flight Controller and maybe also the Ground Station
- Be more resilient to loss of frames

# Serial links

All serial links share the same configuration. The baud rate is `57600`. The airspeed between the RFD900+ modems is 64kbps

A frame on the serial links looks like this:

| Byte number | Description |
| --- | --- |
| 0 | Frame separator: `0x0A` |
| 1 | Frame separator: `0x0D` |
| 2 | Frame ID |
| 3 | Data byte 0 |
| 4 | Data byte 1 |
| [...] | [...] |
| N+3 | Data byte N |

The length of the data field is variable

# CAN Bus

> **Note:** the CAN bus between the Engine Computer and the Flight Controller can be extended to additional boards in future developments

CAN bus: CAN2.0 (FlexCAN) @1Mbit/s with termination 120$\Omega$ resistors on the Flight Controller side and on the Engine Computer side

Base frame format (11 identifier bits)

# Data protocol

The term `ID` is used below to denote `identifier field` of the CAN Bus and byte 2 (`Frame ID`) of a frame over the serial links

The `identifier field` is an 11 bits field but only the 8 lower bits are used to make the data on the CAN Bus as similar as possible to the data on the serial buses. The remaining `ID` values `100` - `7FF` are available for data transfer between on-board systems over the CAN Bus only and cannot be sent to the ground.

Each message on the Telecommand link and the Telemetry link has a unique ID

| ID | Frame type | From | To |
|---|---|---|---|
| `0x00` - `0x0F` | TC | Ground or Flight Controller | Engine Computer |
| `0x10` - `0x7F` | TM | Engine Computer | Ground or Flight Controller  |
| `0x80` - `0x8F` | TC | Ground | Flight Controller |
| `0x90` - `0xEF` | TM | Flight Controller | Ground |
| `0xF0` - `0xFF` | N/A | N/A | N/A |

The `ID` values `0xF0` - `0xFF` are left unused and will be used if new devices are added to the on-board CAN Bus

## Telecommand

The Telecommand link is a low data rate radio link over LoRa at 433 MHz.

### Communication sequence

commands-sequence-no-ec
>Command sequence to the Rocket. Command addressed to the Flight Controller<br>
The source file can be found in [doc/diagrams/command-sequence.xml](diagrams/command-sequence.xml) and edited using [diagrams.net](https://www.diagrams.net/) \[[desktop](https://github.com/jgraph/drawio-desktop/releases)]

commands-sequence-no-ec
>Command sequence to the Rocket. Command addressed to the Engine Controller<br>
The source file can be found in [doc/diagrams/command-sequence.xml](diagrams/command-sequence.xml) and edited using [diagrams.net](https://www.diagrams.net/) \[[desktop](https://github.com/jgraph/drawio-desktop/releases)]

### Commands description

#### Engine Controller

Commands from the Ground Station to the Engine Computer

<table>
<thead>
  <tr>
    <th>ID</th>
    <th>Description</th>
    <th>Data size</th>
    <th>Data</th>
    <th>Comment</th>
  </tr>
</thead>
<tbody>
  <tr>
    <td>0x00</td>
    <td>Time sync<br>Can be sent by FC</td>
    <td>-</td>
    <td>-</td>
    <td></td>
  </tr>
  <tr>
    <td>0x01</td>
    <td>Set power mode</td>
    <td>1 Byte</td>
    <td>TBD enum</td>
    <td>Default state is TBD</td>
  </tr>
  <tr>
    <td>0x02</td>
    <td>Set engine state</td>
    <td>1 Byte</td>
    <td>bit0: is_launch_aborted<br>bit1: is_engine_armed<br>bit2: is_engine_en</td>
    <td>Default state is 0<br>bit0 has absolute priority<br>Must set is_engine_armed to 1 <br>before engine can be enabled</td>
  </tr>
  <tr>
    <td>0x03</td>
    <td>Set liftoff status</td>
    <td>1 Byte</td>
    <td>bit0: is_liftoff_confirmed</td>
    <td>Confirmed by FC sensors</td>
  </tr>
</tbody>
</table>

>**Note:** The LoRa link adds a sizeable delay in the transmission of the commands. This delay makes the "Time sync" frame (`0x00`) inaccurate if sent from the ground. This frame is intended to be sent from the Ground Station for testing purposes and in the absence of GNSS receiver connected to the Flight Controller. When a GNSS receiver is connected to the Flight Controller, the Flight Controller sends a "Time sync" frame based on GNSS time to the Engine Computer over the CAN Bus

Returned data

<table>
<thead>
  <tr>
    <th>ID</th>
    <th>Description</th>
    <th>Data size</th>
    <th>Data</th>
    <th>Comment</th>
  </tr>
</thead>
<tbody>
  <tr>
    <td>0x07</td>
    <td>Power mode<br>Returned after 0x01<br></td>
    <td>1 Byte</td>
    <td>TBD enum</td>
    <td></td>
  </tr>
  <tr>
    <td>0x08</td>
    <td>Engine state<br>Returned after 0x02<br></td>
    <td>1 Byte</td>
    <td>bit0: is_launch_aborted<br>bit1: is_engine_armed<br>bit2: is_engine_en</td>
    <td></td>
  </tr>
  <tr>
    <td>0x09</td>
    <td>Software state</td>
    <td>-</td>
    <td>-</td>
    <td></td>
  </tr>
  <tr>
    <td>0x0A</td>
    <td>Hardware state</td>
    <td>-</td>
    <td>-</td>
    <td></td>
  </tr>
</tbody>
</table>

#### Flight Controller

Commands from the Ground Station to the Flight Controller

<table>
<thead>
  <tr>
    <th>ID</th>
    <th>Description</th>
    <th>Data size</th>
    <th>Data</th>
    <th>Comment</th>
  </tr>
</thead>
<tbody>
  <tr>
    <td>0x80</td>
    <td>Time sync</td>
    <td>-</td>
    <td>-</td>
    <td></td>
  </tr>
  <tr>
    <td>0x81</td>
    <td>Set power mode</td>
    <td>1 Byte</td>
    <td>TBD enum</td>
    <td>Default state is 0</td>
  </tr>
  <tr>
    <td>0x82</td>
    <td>Set radios emitters</td>
    <td>1 Byte</td>
    <td>bit0: is_fpv_en<br>bit1: is_tm_en</td>
    <td>Default state is 0</td>
  </tr>
  <tr>
    <td>0x83</td>
    <td>Set parachute output<br>Used for testing only</td>
    <td>1 Byte</td>
    <td>bit0: is_parachute_armed<br>bit1: is_parachute1_en<br>bit2: is_parachute2_en</td>
    <td>Default state is 0 <br>Must set is_armed to 1 before<br>a parachute can be enabled</td>
  </tr>
</tbody>
</table>

Returned data

<table>
<thead>
  <tr>
    <th>ID</th>
    <th>Description</th>
    <th>Data size</th>
    <th>Data</th>
    <th>Comment</th>
  </tr>
</thead>
<tbody>
  <tr>
    <td>0x87</td>
    <td>Power mode<br>Returned after 0x81</td>
    <td>1 Byte</td>
    <td>TBD enum</td>
    <td></td>
  </tr>
  <tr>
    <td>0x88</td>
    <td>Radio emitters state<br>Returned after 0x82</td>
    <td>1 Byte</td>
    <td>bit0: is_fpv_en<br>bit1: is_tm_en</td>
    <td></td>
  </tr>
  <tr>
    <td>0x89</td>
    <td>Parachute outputs state<br>Returned after 0x83</td>
    <td>1 Byte</td>
    <td>bit0: is_parachute_armed<br>bit1: is_parachute1_en<br>bit2: is_parachute2_en</td>
    <td></td>
  </tr>
  <tr>
    <td rowspan="2">0x8A</td>
    <td rowspan="2">On-board battery voltage<br>Sent every X seconds</td>
    <td rowspan="2">4 Bytes</td>
    <td>voltage_battery_1</td>
    <td>uint16_t, little-endian, in 0.01V</td>
  </tr>
  <tr>
    <td>voltage_battery_2</td>
    <td>uint16_t, little-endian, in 0.01V</td>
  </tr>
  <tr>
    <td>0x8B</td>
    <td>GNSS data</td>
    <td>-</td>
    <td>-</td>
    <td>-</td>
  </tr>
  <tr>
    <td>0x8C</td>
    <td>Software state</td>
    <td>-</td>
    <td>-</td>
    <td>-</td>
  </tr>
</tbody>
</table>

## Telemetry

The Telemetry link is a high data rate radio link over FHSS at 868 MHz. It is technicaly bi-directional but only the downlink capability is used.

### Communication sequence

telemetry-sequence-no-ec
>Telemetry sequence from the Rocket. Telemetry from the Flight Controller<br>
The source file can be found in [doc/diagrams/telemetry-sequence.xml](diagrams/telemetry-sequence.xml) and edited using [diagrams.net](https://www.diagrams.net/) \[[desktop](https://github.com/jgraph/drawio-desktop/releases)]

telemetry-sequence-no-ec
>Telemetry sequence from the Rocket. Telemetry from the Engine Controller<br>
The source file can be found in [doc/diagrams/telemetry-sequence.xml](diagrams/telemetry-sequence.xml) and edited using [diagrams.net](https://www.diagrams.net/) \[[desktop](https://github.com/jgraph/drawio-desktop/releases)]

### Data description

#### Engine Controller

<table>
<thead>
  <tr>
    <th>ID</th>
    <th>Description</th>
    <th>Data size</th>
    <th>Data</th>
    <th>Comment</th>
    <th>Rate</th>
  </tr>
</thead>
<tbody>
  <tr>
    <td>0x10</td>
    <td>Time since boot - millis</td>
    <td>4 Bytes</td>
    <td>ms_since_boot</td>
    <td>uint32_t, little-endian, in ms</td>
    <td></td>
  </tr>
  <tr>
    <td>0x11</td>
    <td>Time since boot - micros</td>
    <td>8 Bytes</td>
    <td>us_since_boot</td>
    <td>uint64_t, little-endian, in us</td>
    <td></td>
  </tr>
</tbody>
</table>

#### Flight Controller

<table>
<thead>
  <tr>
    <th>ID</th>
    <th>Description</th>
    <th>Data size</th>
    <th>Data</th>
    <th>Comment</th>
    <th>Rate</th>
  </tr>
</thead>
<tbody>
  <tr>
    <td>0x90</td>
    <td>Time since boot - millis</td>
    <td>4 Bytes</td>
    <td>ms_since_boot</td>
    <td>uint32_t, little-endian, in ms</td>
    <td></td>
  </tr>
  <tr>
    <td>0x91</td>
    <td>Time since boot - micros</td>
    <td>8 Bytes</td>
    <td>us_since_boot</td>
    <td>uint64_t, little-endian, in us</td>
    <td></td>
  </tr>
  <tr>
    <td>0x92</td>
    <td>GNSS time</td>
    <td>-</td>
    <td>-</td>
    <td>-</td>
    <td>-</td>
  </tr>
  <tr>
    <td></td>
    <td>Software state</td>
    <td>-</td>
    <td>-</td>
    <td>-</td>
    <td>-</td>
  </tr>
  <tr>
    <td></td>
    <td>Hardware state</td>
    <td>1 Byte<br></td>
    <td>bit0: is_parachute_armed<br>bit1: is_parachute1_en<br>bit2: is_parachute2_en<br>bit3: is_fpv_en<br>bit4: is_telemetry_en</td>
    <td>uint8_t</td>
    <td>1 Hz</td>
  </tr>
  <tr>
    <td rowspan="4"></td>
    <td rowspan="4">Static pressure</td>
    <td rowspan="4">16 Bytes</td>
    <td>pressure_1</td>
    <td>int32_t, little-endian, in 0.01 mbar</td>
    <td rowspan="4">1 Hz</td>
  </tr>
  <tr>
    <td>temperature_1</td>
    <td>int32_t, little-endian, in 0.01°C</td>
  </tr>
  <tr>
    <td>pressure_2</td>
    <td>int32_t, little-endian, in 0.01 mbar</td>
  </tr>
  <tr>
    <td>temperature_2</td>
    <td>int32_t, little-endian, in 0.01°C</td>
  </tr>
  <tr>
    <td rowspan="2"></td>
    <td rowspan="2">Static pressure - no temp</td>
    <td rowspan="2">8 bytes</td>
    <td>pressure_1</td>
    <td>int32_t, little-endian, in 0.01 mbar</td>
    <td rowspan="2">10 Hz</td>
  </tr>
  <tr>
    <td>pressure_2</td>
    <td>int32_t, little-endian, in 0.01 mbar</td>
  </tr>
  <tr>
    <td></td>
    <td>IMU</td>
    <td>-</td>
    <td>-</td>
    <td>-</td>
    <td>50 Hz</td>
  </tr>
  <tr>
    <td></td>
    <td>Magnetometer</td>
    <td>-</td>
    <td>-</td>
    <td>-</td>
    <td>-</td>
  </tr>
  <tr>
    <td rowspan="2"></td>
    <td rowspan="2">On-board battery voltage</td>
    <td rowspan="2">4 Bytes</td>
    <td>voltage_battery_1</td>
    <td>uint16_t, little-endian, in 0.01V</td>
    <td rowspan="2">1 Hz</td>
  </tr>
  <tr>
    <td>voltage_battery_2</td>
    <td>uint16_t, little-endian, in 0.01V</td>
  </tr>
  <tr>
    <td></td>
    <td>GNSS data</td>
    <td>-</td>
    <td>-</td>
    <td>-</td>
    <td>-</td>
  </tr>
  <tr>
    <td></td>
    <td>Air speed</td>
    <td>-</td>
    <td>-</td>
    <td>-</td>
    <td>-</td>
  </tr>
  <tr>
    <td></td>
    <td>Air temperature</td>
    <td>-</td>
    <td>-</td>
    <td>-</td>
    <td>-</td>
  </tr>
</tbody>
</table>

#### About time stamps

The data acquisition process is the following:

1. Record the current time (e.g. time since boot)
1. Take a sample from each sensor
1. Send the recorded time
1. Send all the samples in their corresponding frame
1. The time of acquisition for each frame is reconstructed on the Ground Station from the recorded time

This allows to reduce the overhead on the Telemetry link by only sending one time stamp for all the data acquired in one loop.
The error in acquisition time is acceptable as the sampling loop is assumed to be short with respect to the measured phenomena.
All the sensors may not be sampled in every loop or may be sampled without sending the samples to the ground. The sensors that require low sampling rates can simply be sampled and sent every **X** loop

>**Note:** the exact time of acquisition for each sample can still be recorded and stored on the on-board memory

#### About lost frames

Some cases might exist where the time frame is not received on the Ground Station.

On Sigmundr launch (2019), the telemetry frames were ~100 bytes long. It was noticed that when a failure occured, the whole frame was lost instead of just small bits at the beginning or so. This has to do with how the RFD900+ modems handle the data transmission and should be further investigated.

Possible mitigations for early uses of this protocol can be:

- Time stamp all packets at reception time and compare this time with the time frame
- Assume no packet loss (realistic at close range, < 1km with line of sight)
- Group the frames in a big packet (wait and send all at once) like was done on Sigmundr and hope for a pass / fail for one hole sampling loop

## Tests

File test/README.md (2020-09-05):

# Tests <!-- omit in toc -->

This repository uses the platformio unit testing engine to test the software and the hardware.

# Table of content <!-- omit in toc -->

- [Hardware test](#hardware-test)
  - [Requirements](#requirements)
  - [Teensy](#teensy)
    - [Setup](#setup)
    - [What is tested ?](#what-is-tested-)
  - [Arduino nano](#arduino-nano)
    - [Setup](#setup-1)
    - [What is tested ?](#what-is-tested--1)
- [Software test](#software-test)

# Hardware test

The purpose of the hardware test is to make sure that the Flight Controller board performs as intended and that all the chips are 100% working.

## Requirements

- 2x Flight Controller boards (v1.0) with:
  - T:
    - 1x RFM96W LoRa transceiver
    - 1x 433 MHz SMA antenna
    - 1x Teensy 3.6 microcontroller with `5V` & `VUSB` isolated
    - 1x Arduino nano microcontroller (not used yet)
    - Two MS5611 / MPU9250 breakout boards
  - S:
    - 1x Teensy 3.6 microcontroller
- 1x JST-GH / JST-GH 8 pins cable (with wire 5 disconnected)
- 1x JST-GH / JST-GH 6 pins cable (with wires 2&3 inverted)
- 1x micro USB to USB cable
- 1x mini USB to USB cable
- 1x 2S LiPo battery with an XT-30 connector
- 1x 3S LiPo battery with an XT-60 connector

**ALWAYS connect an antenna on all boards that have a Lora chip (U3)**

## Teensy

Sources :

`test/hardware_test_teensy/` -> used to test all the I/O<br>
`src/test_companion_teensy.cpp` -> used to help test the data links, works on a secondary board

### Setup

Let's call the board to test 'T' and the secondary board 'S'

- Connect 'S' to your computer with the micro USB cable
- Upload the companion code on 'S' using the platformio shell

```sh
platformio run -t upload -e teensy_test
```

- Disconnect the micro USB cable from 'S'
- Connect 'S' and 'T' (only one at a time):
  -  with the JST-GH 8 pins cable on J6 [to test the CAN bus]
  -  with the JST-GH 6 pins cable on J1, J2, or J3 [to test the Serial ports]
- Connect the 2S LiPo to 'T'
- Connect the 3S LiPo to 'T'
- Connect 'T' to your computer with the micro USB cable
- Upload the test code on 'T' using the platformio shell

```sh
platformio test -e teensy_test -f hardware_test_teensy
# or
platformio test -e teensy_test_silent -f hardware_test_teensy # no buzzer sound
```

- Look at the output in the terminal

### What is tested ?

Currently:

- MS5611
- RFM96W
- CAN Bus
- Serial ports
- Buzzer
- RGB Leds
- Parachute outputs
- Mosfet for J2 power line (Telemetry modem)
- Mosfet for J4 power line (FPV)

Missing:

- MPU9250
- NEO M9N
- I²C
- Flash memory
- Interrupts for liftoff detection
- Temperature sensors

## Arduino nano

Sources :

`test/hardware_test_nano/` -> used to test all the I/O<br>

### Setup

Only one board ('T') is needed

- Connect the 2S LiPo to 'T'
- Connect the 3S LiPo to 'T'
- Connect 'T' to your computer with the mini USB cable
- Upload the test code on 'T' using the platformio shell

```sh
platformio test -e nano_test -f hardware_test_nano
```

- Look at the output in the terminal

### What is tested ?

- Buzzer
- Parachute outputs

# Software test

*TODO: make the embedded software compatible with unit testing and write unit tests for it*

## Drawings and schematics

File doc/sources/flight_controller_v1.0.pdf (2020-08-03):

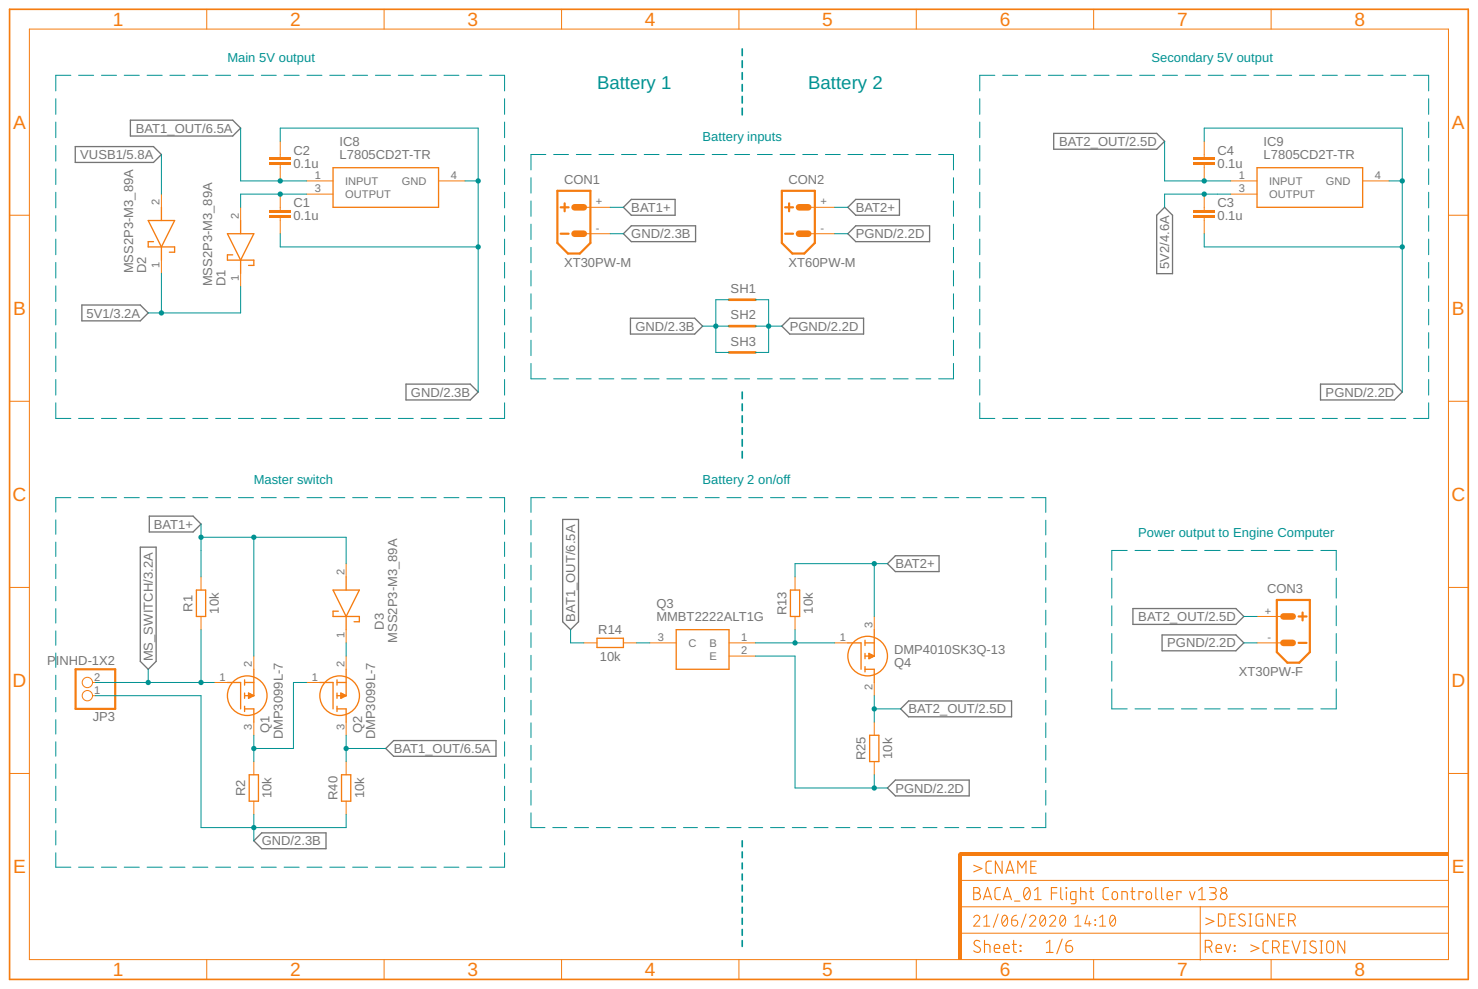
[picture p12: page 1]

Power output to Engine Computer

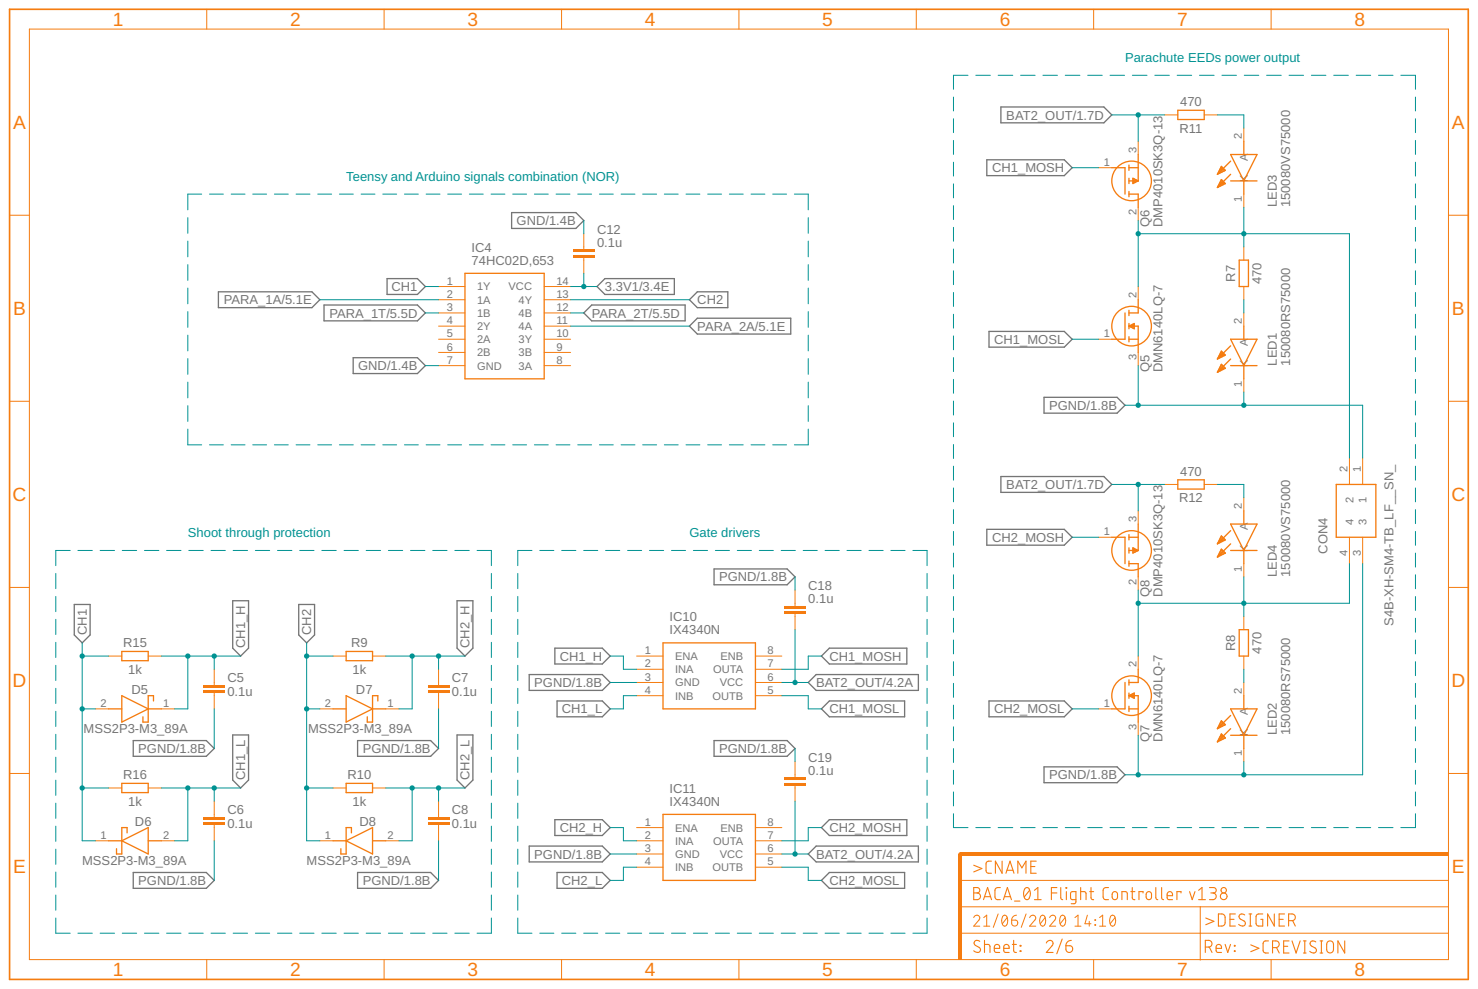
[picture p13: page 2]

Parachute EEDs power output

Teensy and Arduino signals combination (NOR)

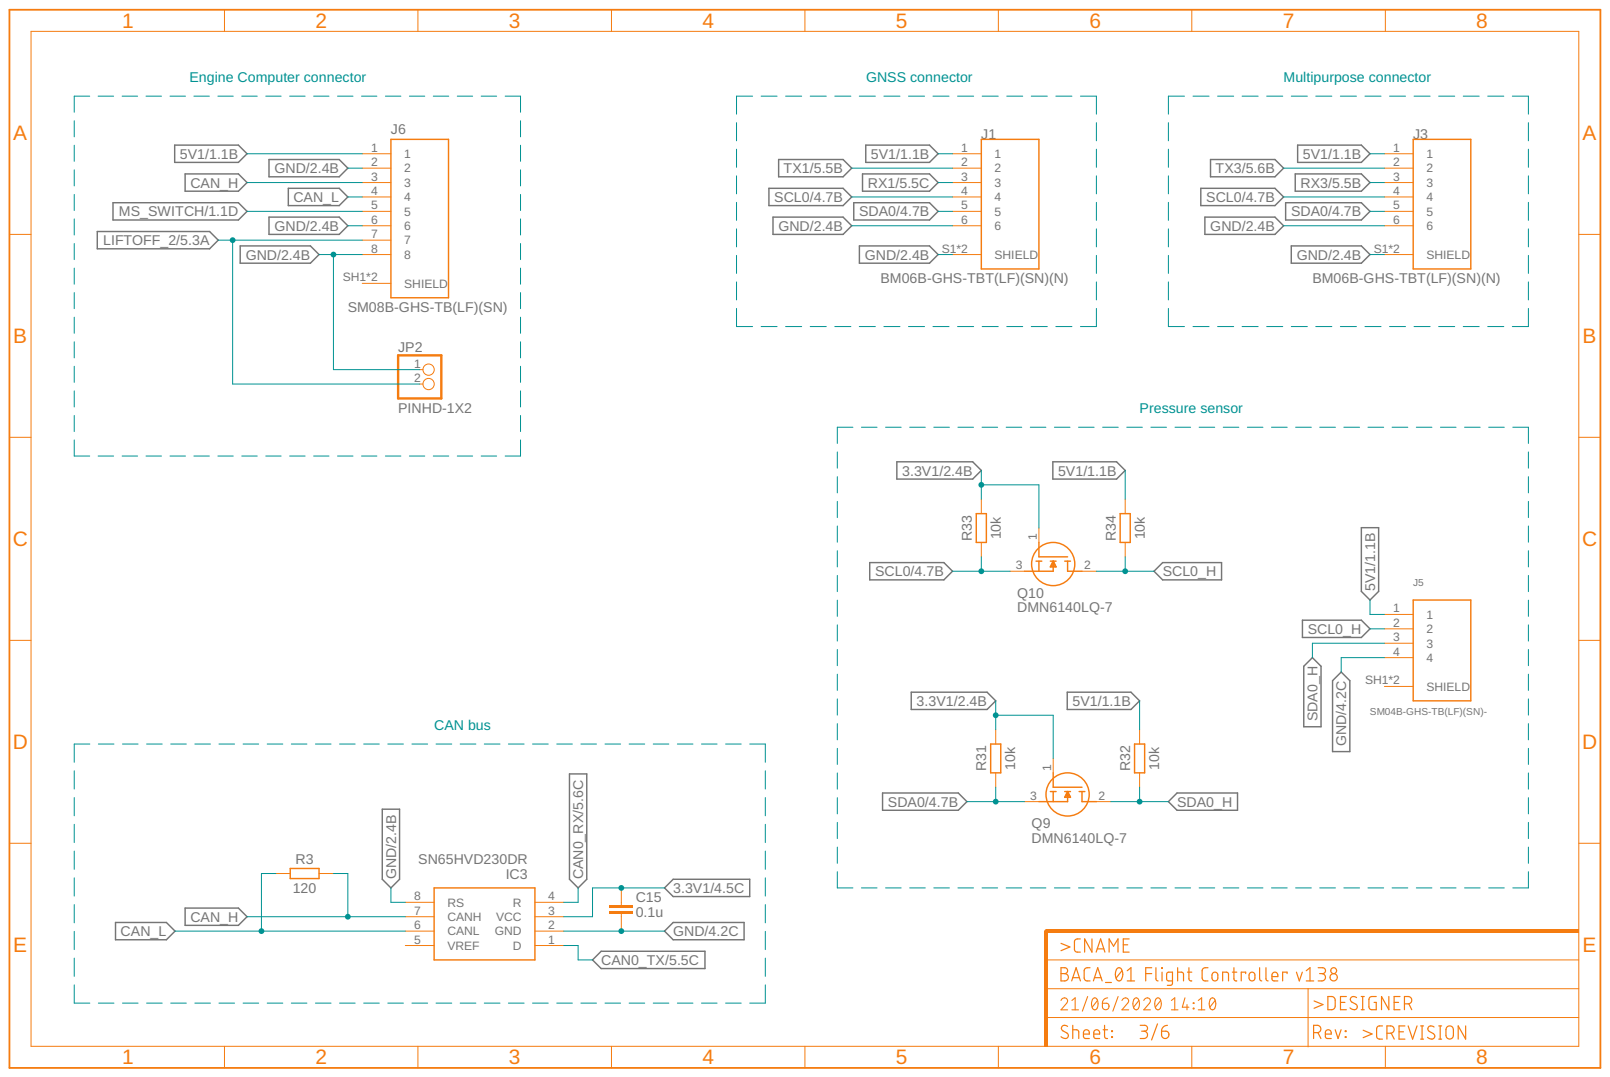
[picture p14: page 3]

BM06B-GHS-TBT(LF)(SN)(N)

SM08B-GHS-TB(LF)(SN)

SM04B-GHS-TB(LF)(SN)- DMN6140LQ-7

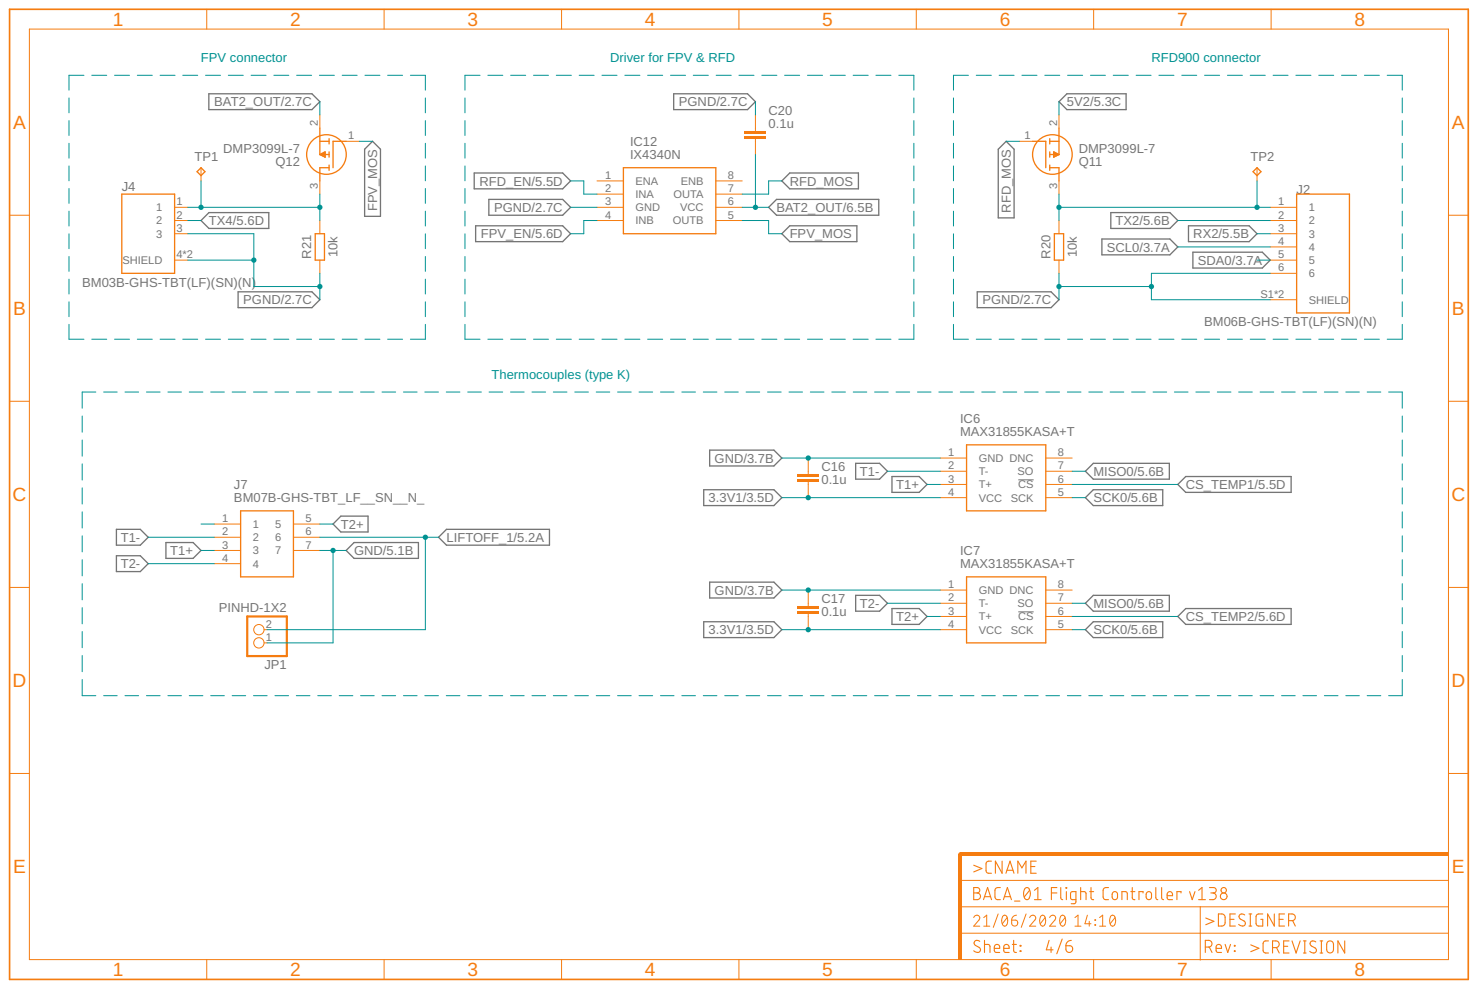
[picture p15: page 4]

BM03B-GHS-TBT(LF)(SN)(N)

BM06B-GHS-TBT(LF)(SN)(N)

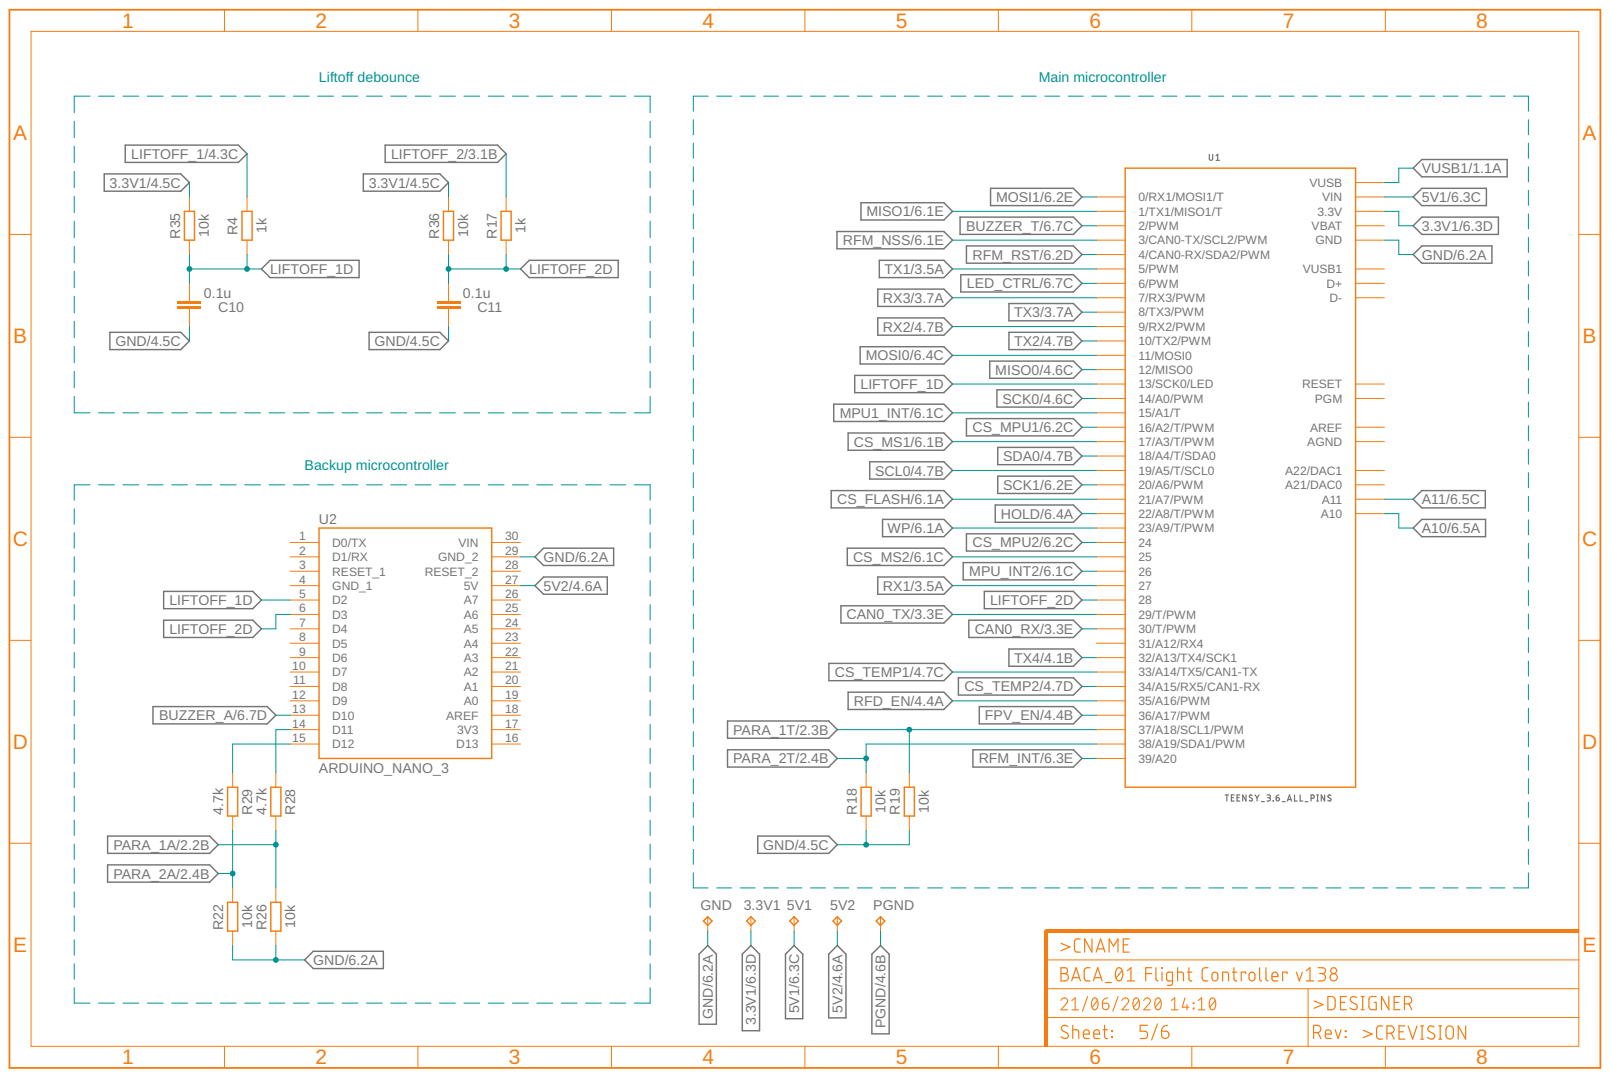
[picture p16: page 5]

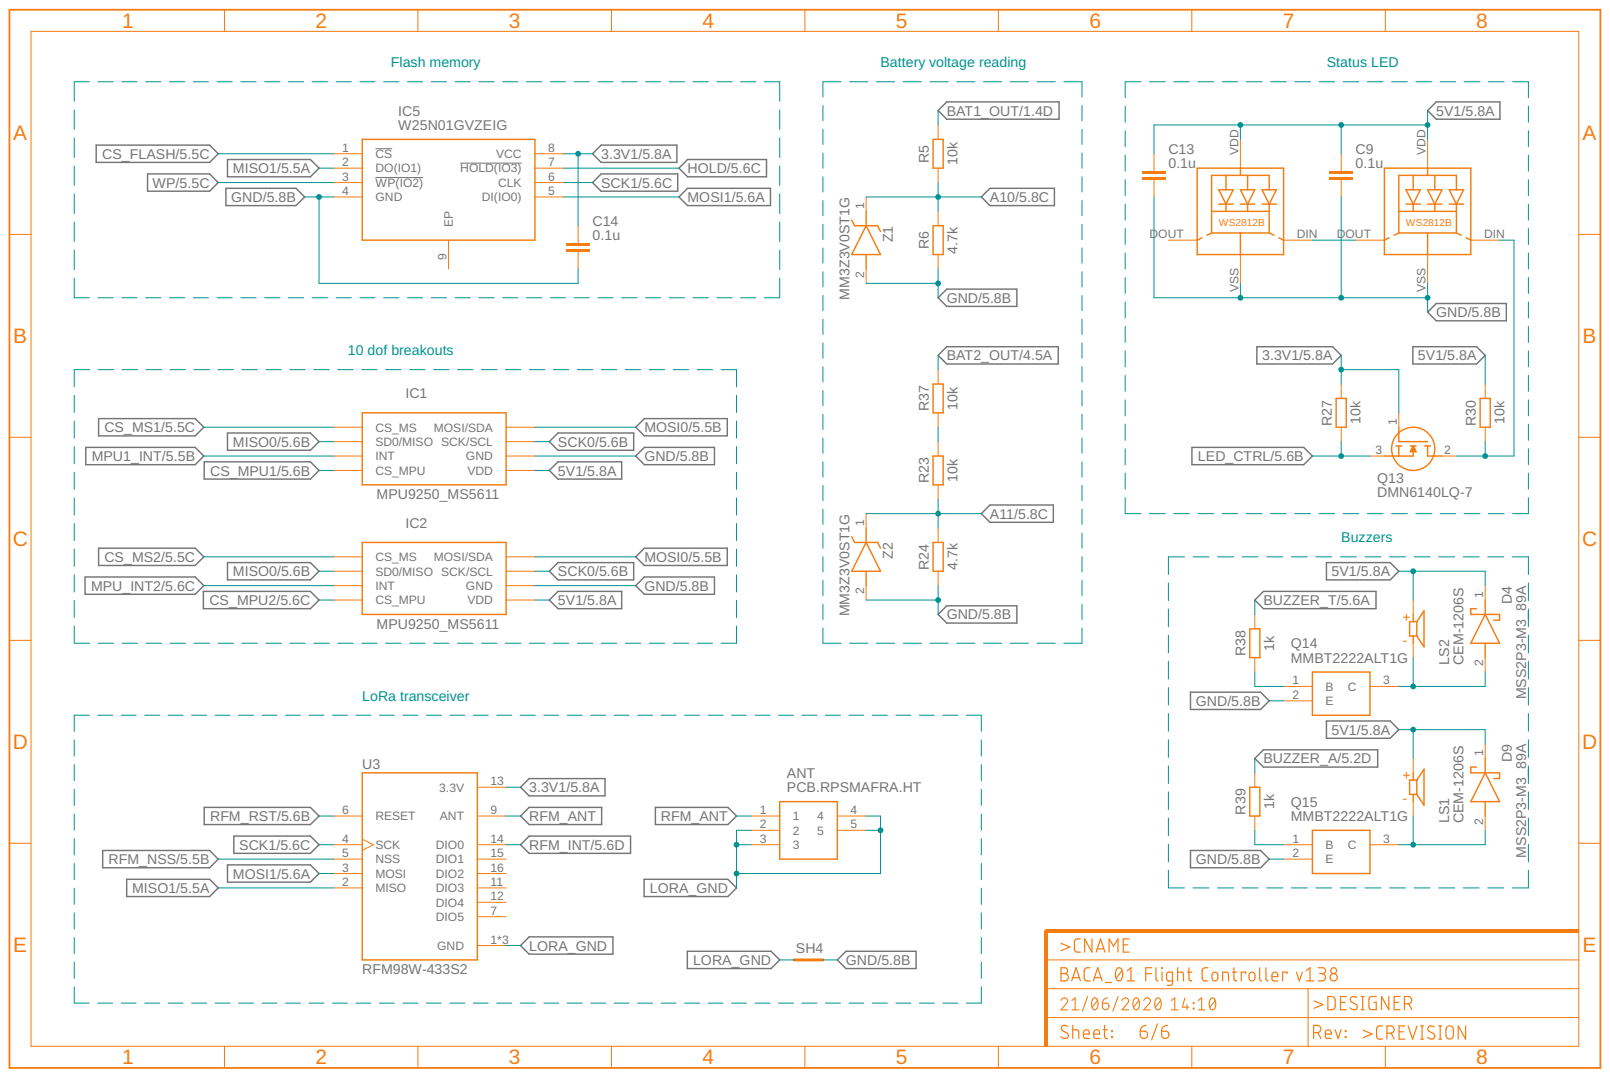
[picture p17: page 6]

SCK/SCL MOSI/SDA

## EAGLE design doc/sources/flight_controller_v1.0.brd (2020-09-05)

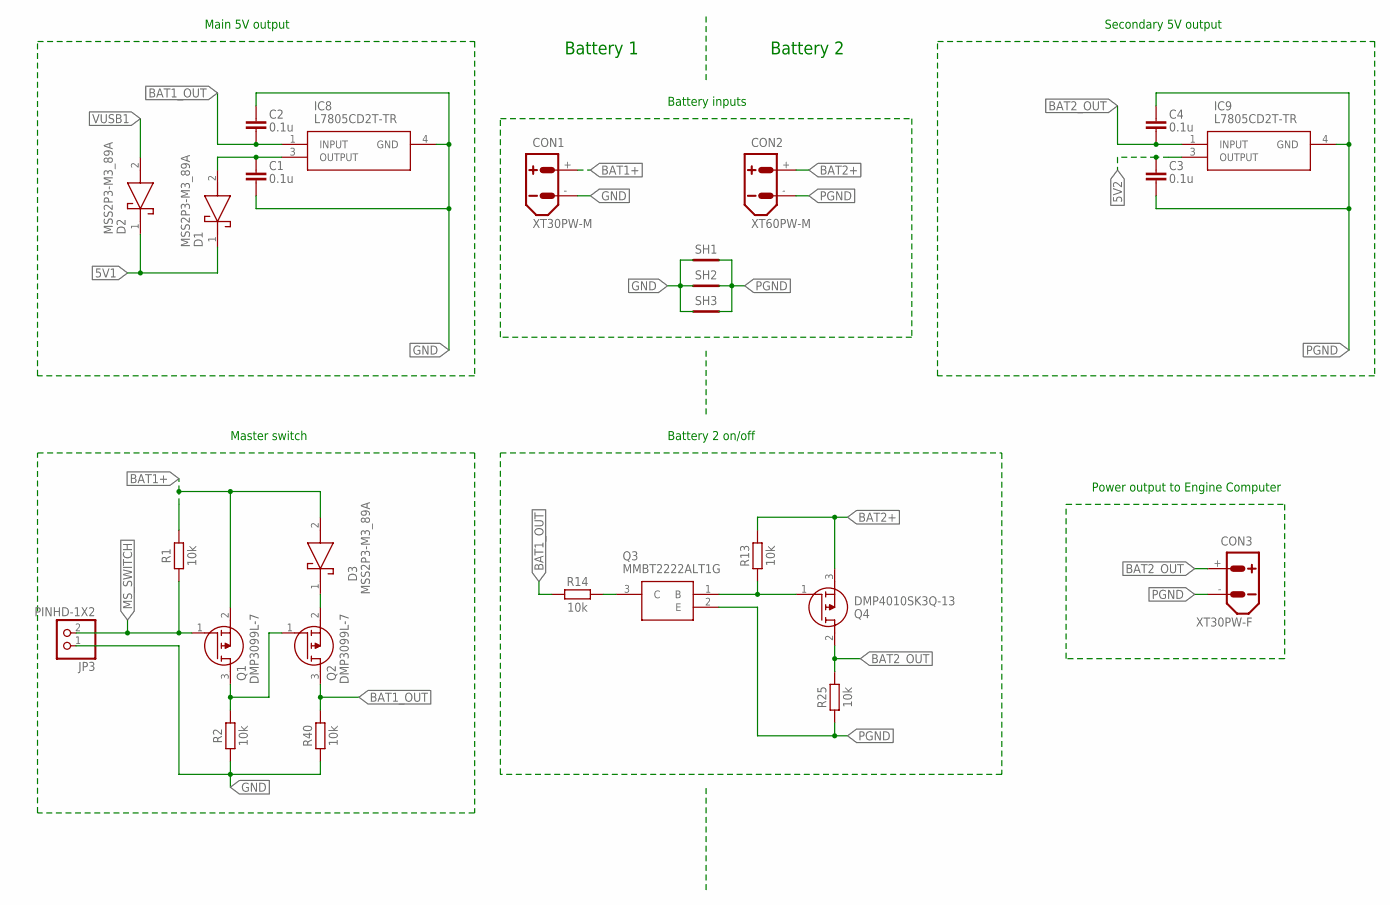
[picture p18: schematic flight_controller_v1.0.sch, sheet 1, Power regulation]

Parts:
C1, C2, C3, C4: 0.1u; CAPC2012X110
CON1: XT30PW-M
CON2: XT60PW-M
CON3: XT30PW-F
D1, D2, D3: MSS2P3-M3_89A; MSS2P3M389A
IC8, IC9: L7805CD2T-TR; TO254P1542X460-3N
JP3: PINHD-1X2; 1X02
Q1, Q2: DMP3099L-7; SOT96P240X120-3N
Q3: MMBT2222ALT1G; SOT96P237X111-3N
Q4: DMP4010SK3Q-13; SBR6100CTL13
R1, R2, R13, R14, R25, R40: 10k; RESC2012X65
SH1, SH2, SH3: SHORT-HT5; SHORT_TOP-50

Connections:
5V1: D1.1 (K), D2.1 (K); also elsewhere on the board
5V2: C3.1, IC9.3 (OUTPUT); also elsewhere on the board
BAT1+: CON1.+, D3.2 (A), Q1.2 (S), R1.2
BAT1_OUT: C2.2, IC8.1 (INPUT), Q2.3 (D), R14.1, R40.2; also elsewhere on the board
BAT2+: CON2.+, Q4.3 (S), R13.2
BAT2_OUT: C4.2, CON3.+, IC9.1 (INPUT), Q4.2 (D), R25.2; also elsewhere on the board
GND: C1.2, C2.1, CON1.-, IC8.4 (GND), JP3.1, R2.1, R40.1, SH1.1, SH2.1, SH3.1; also elsewhere on the board
MS_SWITCH: JP3.2, Q1.1 (G), R1.1; also elsewhere on the board
unnamed: Q1.3 (D), Q2.1 (G), R2.2
unnamed: Q3.1 (B), Q4.1 (G), R13.1
unnamed: Q3.3 (C), R14.2
unnamed: C1.1, D1.2 (A), IC8.3 (OUTPUT)
unnamed: D3.1 (K), Q2.2 (S)
PGND: C3.2, C4.1, CON2.-, CON3.-, IC9.4 (GND), Q3.2 (E), R25.1, SH1.2, SH2.2, SH3.2; also elsewhere on the board
VUSB1: D2.2 (A); also elsewhere on the board

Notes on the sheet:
Main 5V output
Battery inputs
Master switch
Secondary 5V output
Battery 2 on/off
Battery 1
Battery 2
Power output to Engine Computer

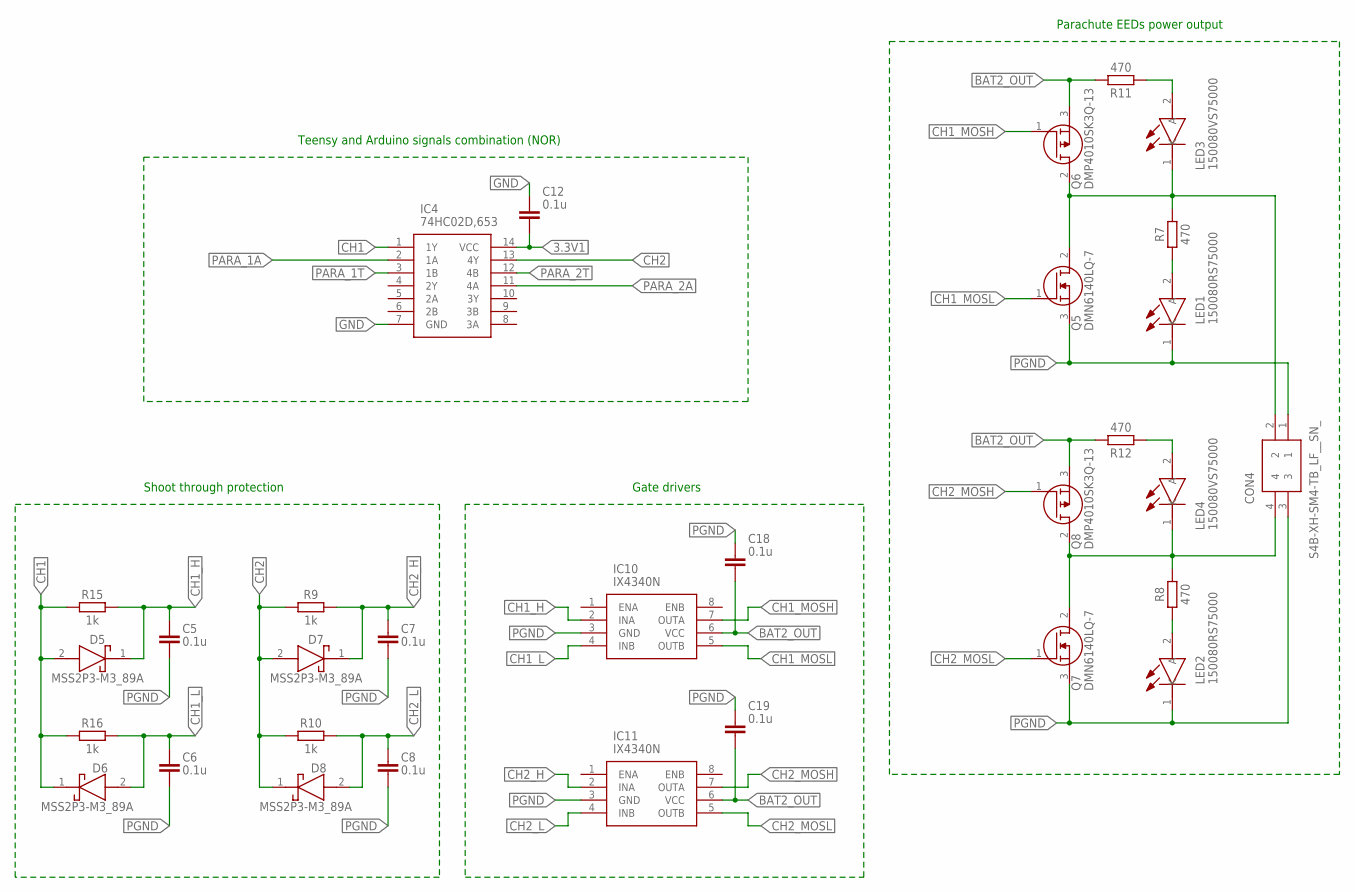
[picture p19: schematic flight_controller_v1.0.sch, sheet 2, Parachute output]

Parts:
C5, C6, C7, C8, C12, C18, C19: 0.1u; CAPC2012X110
CON4: S4B-XH-SM4-TB_LF__SN_; S4B-XH-SM4-TB
D5, D6, D7, D8: MSS2P3-M3_89A; MSS2P3M389A
IC4: 74HC02D,653; SOIC127P600X175-14N
IC10, IC11: IX4340N; SOIC127P600X175-8N
LED1, LED2: 150080RS75000; LEDC2012X80N
LED3, LED4: 150080VS75000; LEDC2012X80N
Q5, Q7: DMN6140LQ-7; SOT96P240X110-3N
Q6, Q8: DMP4010SK3Q-13; SBR6100CTL13
R7, R8, R11, R12: 470; RESC2012X65
R9, R10, R15, R16: 1k; RESC2012X65

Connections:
3.3V1: C12.2, IC4.14 (VCC); also elsewhere on the board
BAT2_OUT: C18.2, C19.2, IC10.6 (VCC), IC11.6 (VCC), Q6.3 (S), Q8.3 (S), R11.2, R12.2; also elsewhere on the board
CH1: D5.2 (A), D6.1 (K), IC4.1 (1Y), R15.1, R16.1
CH1_H: C5.1, D5.1 (K), IC10.2 (INA), R15.2
CH1_L: C6.1, D6.2 (A), IC10.4 (INB), R16.2
CH1_MOSH: IC10.7 (OUTA), Q6.1 (G)
CH1_MOSL: IC10.5 (OUTB), Q5.1 (G)
CH2: D7.2 (A), D8.1 (K), IC4.13 (4Y), R9.1, R10.1
CH2_H: C7.1, D7.1 (K), IC11.2 (INA), R9.2
CH2_L: C8.1, D8.2 (A), IC11.4 (INB), R10.2
CH2_MOSH: IC11.7 (OUTA), Q8.1 (G)
CH2_MOSL: IC11.5 (OUTB), Q7.1 (G)
GND: C12.1, IC4.7 (GND); also elsewhere on the board
unnamed: CON4.2, LED3.1 (K), Q5.2 (D), Q6.2 (D), R7.2
unnamed: LED1.2 (A), R7.1
unnamed: CON4.4, LED4.1 (K), Q7.2 (D), Q8.2 (D), R8.2
unnamed: LED2.2 (A), R8.1
unnamed: LED3.2 (A), R11.1
unnamed: LED4.2 (A), R12.1
PARA_1A: IC4.2 (1A); also elsewhere on the board
PARA_1T: IC4.3 (1B); also elsewhere on the board
PARA_2A: IC4.11 (4A); also elsewhere on the board
PARA_2T: IC4.12 (4B); also elsewhere on the board
PGND: C5.2, C6.2, C7.2, C8.2, C18.1, C19.1, CON4.1, CON4.3, IC10.3 (GND), IC11.3 (GND), LED1.1 (K), LED2.1 (K), Q5.3 (S), Q7.3 (S); also elsewhere on the board

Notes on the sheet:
Gate drivers
Parachute EEDs power output
Shoot through protection
Teensy and Arduino signals combination (NOR)

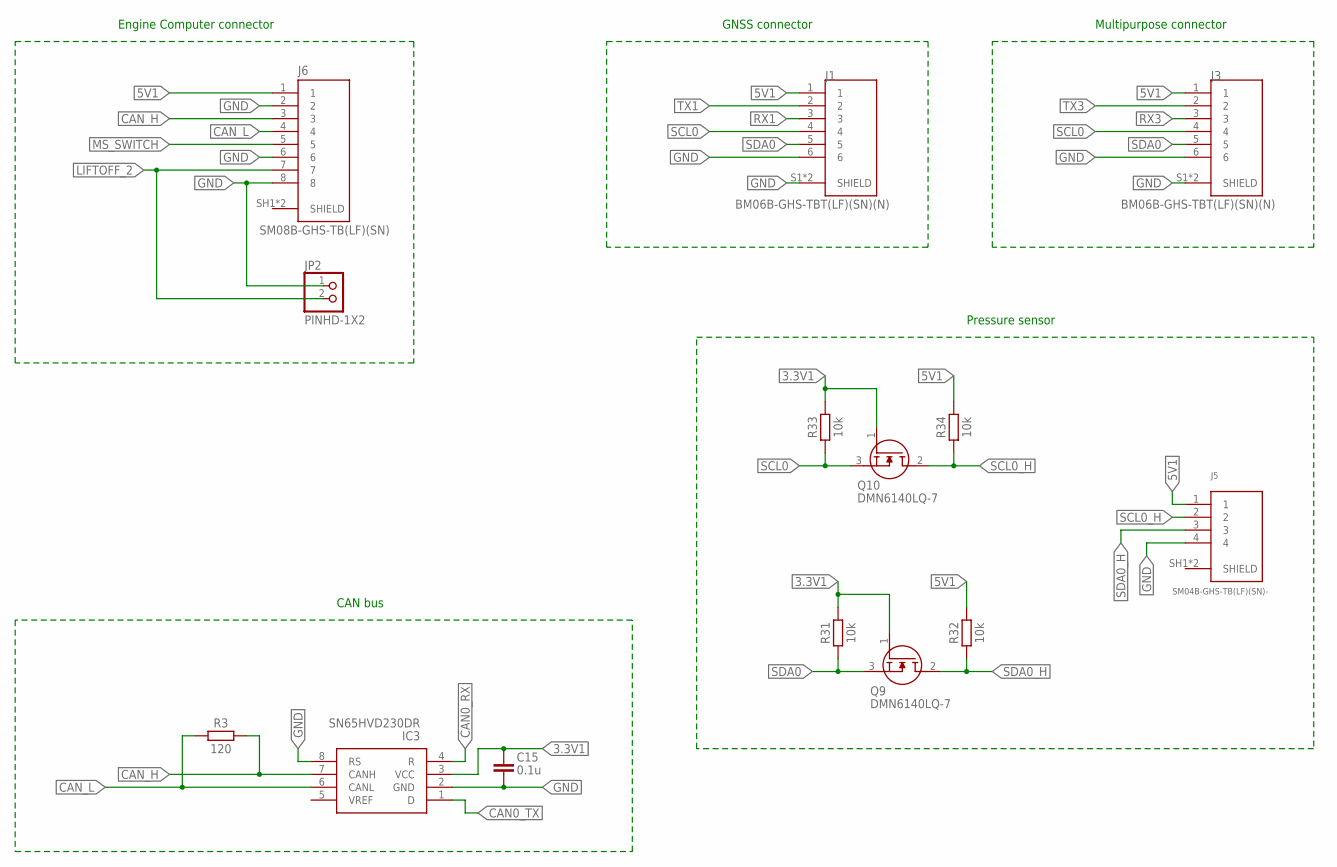
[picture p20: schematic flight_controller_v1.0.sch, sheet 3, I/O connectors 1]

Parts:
C15: 0.1u; CAPC2012X110
IC3: SN65HVD230DR; SOT127P600X175-8N
J1, J3: BM06B-GHS-TBT(LF)(SN)(N); JST_BM06B-GHS-TBT(LF)(SN)(N)
J5: SM04B-GHS-TB(LF)(SN)-; JST_SM04B-GHS-TB(LF)(SN)-
J6: SM08B-GHS-TB(LF)(SN); JST_SM08B-GHS-TB(LF)(SN)
JP2: PINHD-1X2; 1X02
Q9, Q10: DMN6140LQ-7; SOT96P240X110-3N
R3: 120; RESC2012X65
R31, R32, R33, R34: 10k; RESC2012X65

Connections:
3.3V1: C15.1, IC3.3 (VCC), Q9.1 (G), Q10.1 (G), R31.2, R33.2; also elsewhere on the board
5V1: J1.1, J3.1, J5.1, J6.1, R32.2, R34.2; also elsewhere on the board
CAN0_RX: IC3.4 (R); also elsewhere on the board
CAN0_TX: IC3.1 (D); also elsewhere on the board
CAN_H: IC3.7 (CANH), J6.3, R3.2
CAN_L: IC3.6 (CANL), J6.4, R3.1
GND: C15.2, IC3.2 (GND), IC3.8 (RS), J1.6, J1.S1 (SHIELD), J1.S2 (SHIELD), J3.6, J3.S1 (SHIELD), J3.S2 (SHIELD), J5.4, J6.2, J6.6, J6.8, JP2.1; also elsewhere on the board
LIFTOFF_2: J6.7, JP2.2; also elsewhere on the board
MS_SWITCH: J6.5; also elsewhere on the board
RX1: J1.3; also elsewhere on the board
RX3: J3.3; also elsewhere on the board
SCL0: J1.4, J3.4, Q10.3 (S), R33.1; also elsewhere on the board
SCL0_H: J5.2, Q10.2 (D), R34.1
SDA0: J1.5, J3.5, Q9.3 (S), R31.1; also elsewhere on the board
SDA0_H: J5.3, Q9.2 (D), R32.1
SHIELD: J5.SH1 (SHIELD), J5.SH2 (SHIELD)
TX1: J1.2; also elsewhere on the board
TX3: J3.2; also elsewhere on the board

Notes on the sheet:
CAN bus
GNSS connector
Engine Computer connector
Multipurpose connector
Pressure sensor

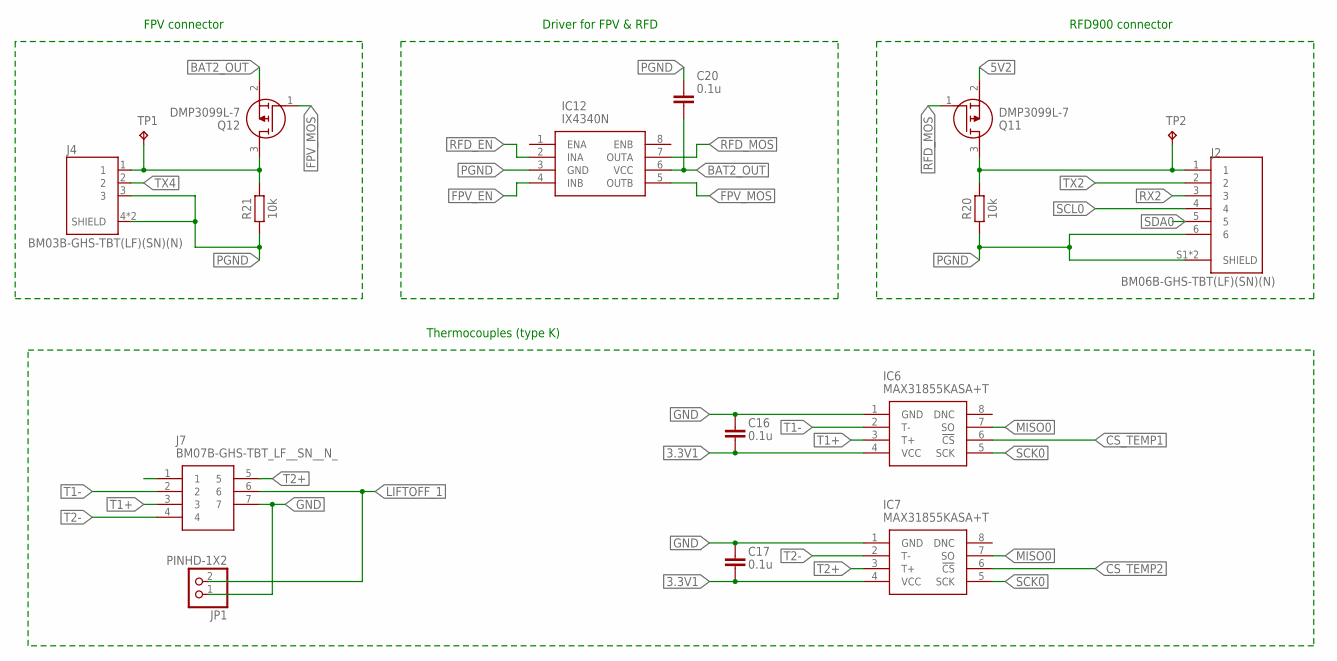
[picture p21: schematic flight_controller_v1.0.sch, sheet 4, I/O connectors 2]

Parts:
C16, C17, C20: 0.1u; CAPC2012X110
IC6, IC7: MAX31855KASA+T; SOIC127P600X175-8N
IC12: IX4340N; SOIC127P600X175-8N
J2: BM06B-GHS-TBT(LF)(SN)(N); JST_BM06B-GHS-TBT(LF)(SN)(N)
J4: BM03B-GHS-TBT(LF)(SN)(N); CONN_BM03B-GHS-TBT(LF)(SN)(N)
J7: BM07B-GHS-TBT_LF__SN__N_; BM07B-GHS-TBT
JP1: PINHD-1X2; 1X02
Q11, Q12: DMP3099L-7; SOT96P240X120-3N
R20, R21: 10k; RESC2012X65
TP1, TP2: TPB1,27; B1,27

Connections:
3.3V1: C16.2, C17.2, IC6.4 (VCC), IC7.4 (VCC); also elsewhere on the board
5V2: Q11.2 (S); also elsewhere on the board
BAT2_OUT: C20.2, IC12.6 (VCC), Q12.2 (S); also elsewhere on the board
CS_TEMP1: IC6.6 (!CS); also elsewhere on the board
CS_TEMP2: IC7.6 (!CS); also elsewhere on the board
FPV_EN: IC12.4 (INB); also elsewhere on the board
FPV_MOS: IC12.5 (OUTB), Q12.1 (G)
GND: C16.1, C17.1, IC6.1 (GND), IC7.1 (GND), J7.7, JP1.1; also elsewhere on the board
LIFTOFF_1: J7.6, JP1.2; also elsewhere on the board
MISO0: IC6.7 (SO), IC7.7 (SO); also elsewhere on the board
unnamed: J2.1, Q11.3 (D), R20.2, TP2.TP
unnamed: J4.1, Q12.3 (D), R21.2, TP1.TP
PGND: C20.1, IC12.3 (GND), J2.6, J2.S1 (SHIELD), J2.S2 (SHIELD), J4.3, J4.4 (SHIELD), J4.5 (SHIELD), R20.1, R21.1; also elsewhere on the board
RFD_EN: IC12.2 (INA); also elsewhere on the board
RFD_MOS: IC12.7 (OUTA), Q11.1 (G)
RX2: J2.3; also elsewhere on the board
SCK0: IC6.5 (SCK), IC7.5 (SCK); also elsewhere on the board
SCL0: J2.4; also elsewhere on the board
SDA0: J2.5; also elsewhere on the board
T1+: IC6.3 (T+), J7.3
T1-: IC6.2 (T-), J7.2
T2+: IC7.3 (T+), J7.5
T2-: IC7.2 (T-), J7.4
TX2: J2.2; also elsewhere on the board
TX4: J4.2; also elsewhere on the board

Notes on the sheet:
FPV connector
Driver for FPV & RFD
RFD900 connector
Thermocouples (type K)

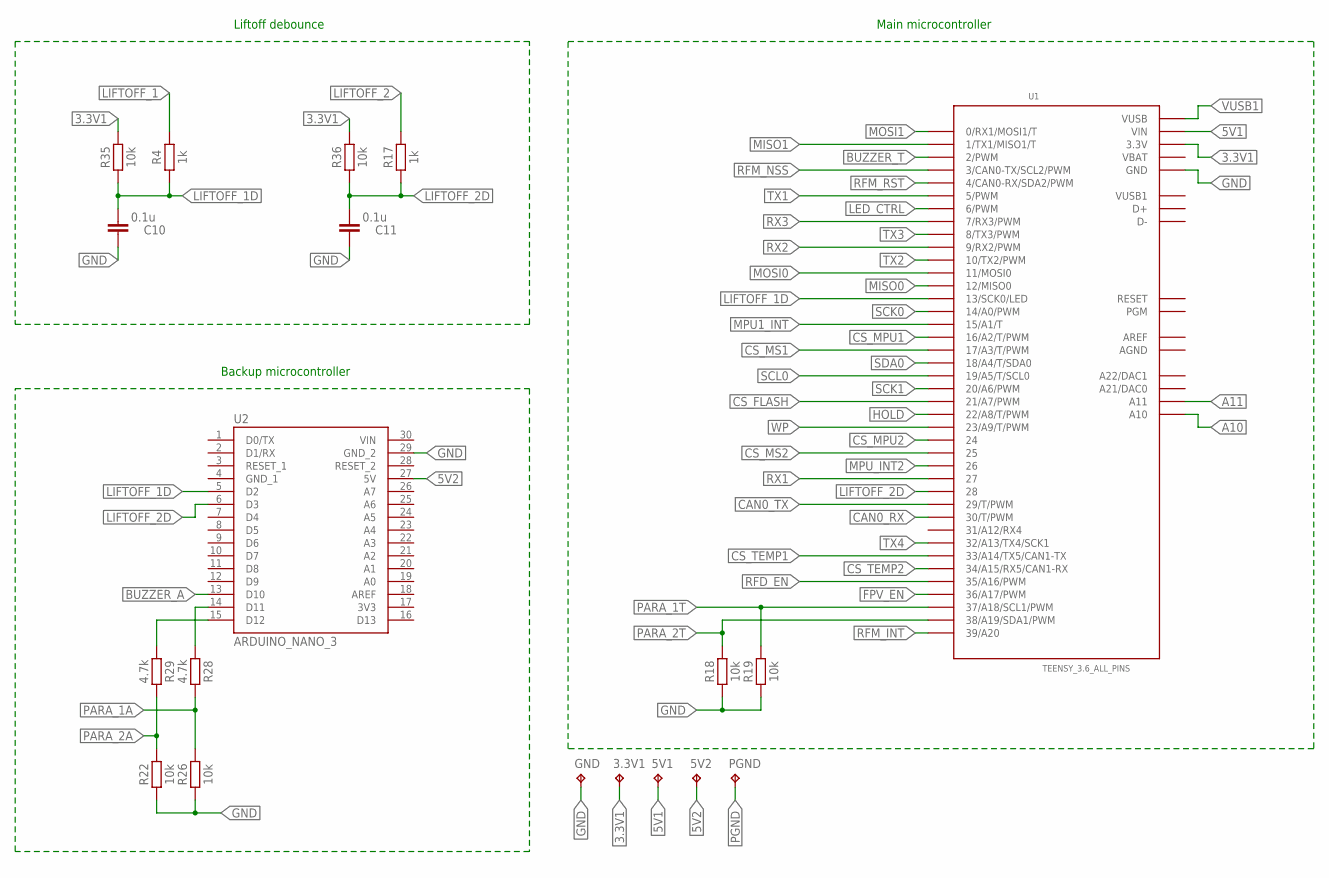
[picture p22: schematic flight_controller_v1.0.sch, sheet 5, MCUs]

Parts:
3.3V1, 5V1, 5V2: TPB1,27; B1,27
C10, C11: 0.1u; CAPC2012X110
GND: TPB1,27; B1,27
PGND: TPB1,27; B1,27
R4, R17: 1k; RESC2012X65
R18, R19, R22, R26, R35, R36: 10k; RESC2012X65
R28, R29: 4.7k; RESC2012X65
U1: TEENSY_3.6_ALL_PINS
U2: ARDUINO_NANO_3; MODULE_A000005

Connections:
3.3V1: 3.3V1.TP, R35.2, R36.2, U1.3.3V, U1.3.3V3 (3.3V), U1.3.3V4 (3.3V); also elsewhere on the board
3V3: U2.17 (3V3)
5V1: 5V1.TP, U1.VIN; also elsewhere on the board
5V2: 5V2.TP, U2.27 (5V); also elsewhere on the board
A10: U1.A10; also elsewhere on the board
A11: U1.A11; also elsewhere on the board
AGND: U1.AGND
AREF: U1.AREF
BUZZER_A: U2.13 (D10); also elsewhere on the board
BUZZER_T: U1.2 (2/PWM); also elsewhere on the board
CAN0_RX: U1.30 (30/T/PWM); also elsewhere on the board
CAN0_TX: U1.29 (29/T/PWM); also elsewhere on the board
CS_FLASH: U1.21/A7 (21/A7/PWM); also elsewhere on the board
CS_MPU1: U1.16/A2 (16/A2/T/PWM); also elsewhere on the board
CS_MPU2: U1.24; also elsewhere on the board
CS_MS1: U1.17/A3 (17/A3/T/PWM); also elsewhere on the board
CS_MS2: U1.25; also elsewhere on the board
CS_TEMP1: U1.33/A14 (33/A14/TX5/CAN1-TX); also elsewhere on the board
CS_TEMP2: U1.34/A15 (34/A15/RX5/CAN1-RX); also elsewhere on the board
FPV_EN: U1.36/A17 (36/A17/PWM); also elsewhere on the board
GND: C10.2, C11.2, GND.TP, R18.1, R19.1, R22.1, R26.1, U1.GND, U1.GND1 (GND), U1.GND3 (GND), U1.GND4 (GND), U1.GND6 (GND), U2.29 (GND_2); also elsewhere on the board
GND_1: U2.4 (GND_1)
HOLD: U1.22/A8 (22/A8/T/PWM); also elsewhere on the board
LED_CTRL: U1.6 (6/PWM); also elsewhere on the board
LIFTOFF_1: R4.2; also elsewhere on the board
LIFTOFF_1D: C10.1, R4.1, R35.1, U1.13 (13/SCK0/LED), U2.5 (D2)
LIFTOFF_2: R17.2; also elsewhere on the board
LIFTOFF_2D: C11.1, R17.1, R36.1, U1.28, U2.6 (D3)
MISO0: U1.12 (12/MISO0); also elsewhere on the board
MISO1: U1.1 (1/TX1/MISO1/T); also elsewhere on the board
MOSI0: U1.11 (11/MOSI0); also elsewhere on the board
MOSI1: U1.0 (0/RX1/MOSI1/T); also elsewhere on the board
MPU1_INT: U1.15/A1 (15/A1/T); also elsewhere on the board
MPU_INT2: U1.26; also elsewhere on the board
unnamed: R28.1, U2.14 (D11)
unnamed: R29.1, U2.15 (D12)
PARA_1A: R26.2, R28.2; also elsewhere on the board
PARA_1T: R19.2, U1.37/A18 (37/A18/SCL1/PWM); also elsewhere on the board
PARA_2A: R22.2, R29.2; also elsewhere on the board
PARA_2T: R18.2, U1.38/A19 (38/A19/SDA1/PWM); also elsewhere on the board
PGND: PGND.TP; also elsewhere on the board
RFD_EN: U1.35/A16 (35/A16/PWM); also elsewhere on the board
RFM_INT: U1.39/A20; also elsewhere on the board
RFM_NSS: U1.3 (3/CAN0-TX/SCL2/PWM); also elsewhere on the board
RFM_RST: U1.4 (4/CAN0-RX/SDA2/PWM); also elsewhere on the board
RX1: U1.27; also elsewhere on the board
RX2: U1.9 (9/RX2/PWM); also elsewhere on the board
RX3: U1.7 (7/RX3/PWM); also elsewhere on the board
SCK0: U1.14/A0 (14/A0/PWM); also elsewhere on the board
SCK1: U1.20/A6 (20/A6/PWM); also elsewhere on the board
SCL0: U1.19/A5 (19/A5/T/SCL0); also elsewhere on the board
SDA0: U1.18/A4 (18/A4/T/SDA0); also elsewhere on the board
TX1: U1.5 (5/PWM); also elsewhere on the board
TX2: U1.10 (10/TX2/PWM); also elsewhere on the board
TX3: U1.8 (8/TX3/PWM); also elsewhere on the board
TX4: U1.32/A13 (32/A13/TX4/SCK1); also elsewhere on the board
VBAT: U1.VBAT
VIN: U2.30 (VIN)
VUSB1: U1.VUSB, U1.VUSB1; also elsewhere on the board
WP: U1.23/A9 (23/A9/T/PWM); also elsewhere on the board

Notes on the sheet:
Main microcontroller
Backup microcontroller
Liftoff debounce

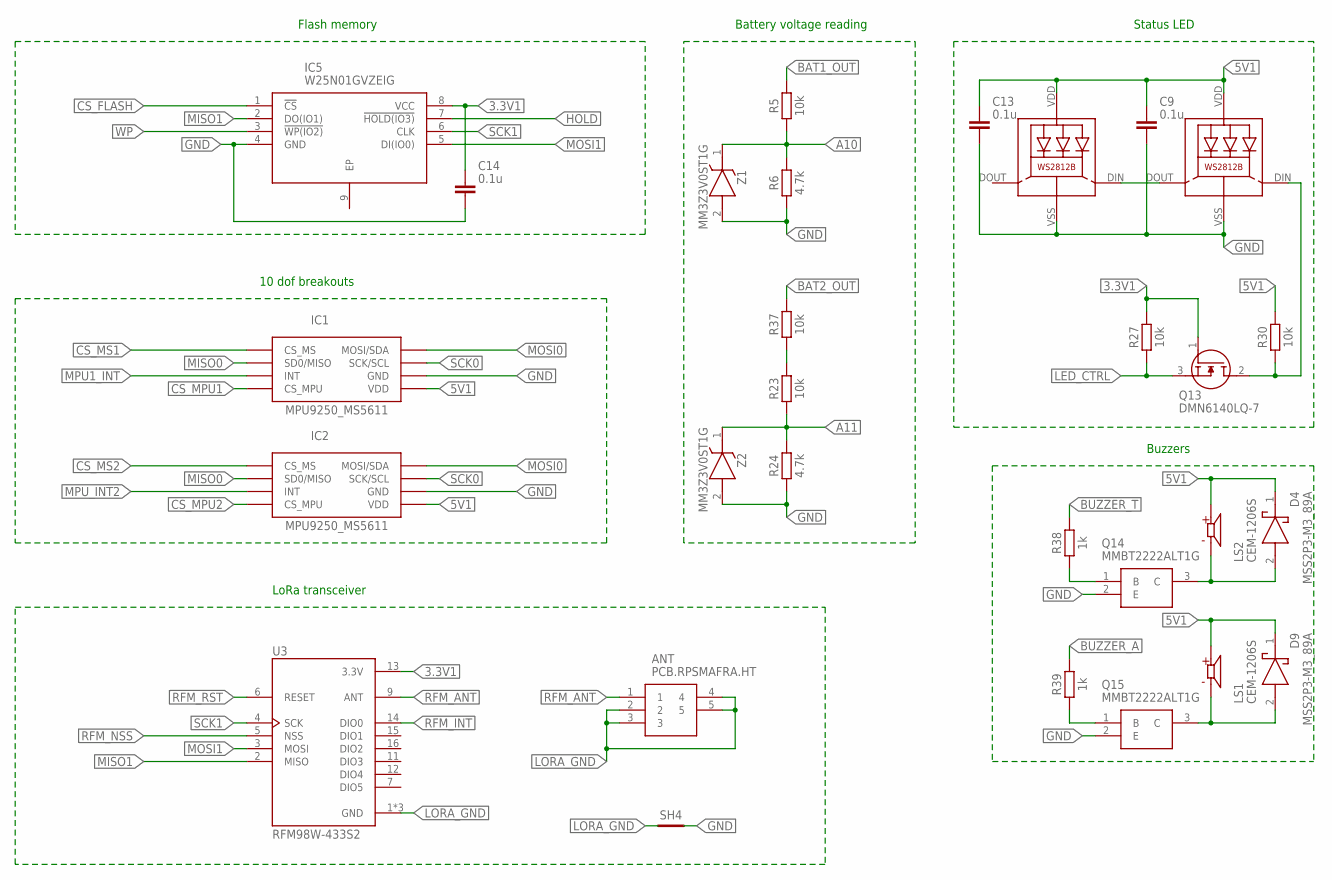
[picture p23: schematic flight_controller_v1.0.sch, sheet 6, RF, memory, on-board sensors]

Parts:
ANT: PCB.RPSMAFRA.HT; PCBRPSMAFRAHT
C9, C13, C14: 0.1u; CAPC2012X110
D4, D9: MSS2P3-M3_89A; MSS2P3M389A
IC1, IC2: MPU9250_MS5611; 2X4PIN
IC5: W25N01GVZEIG; SON127P800X600X80-9N
LED5, LED6: WS2812B
LS1, LS2: CEM-1206S; CUI_CEM-1206S
Q13: DMN6140LQ-7; SOT96P240X110-3N
Q14, Q15: MMBT2222ALT1G; SOT96P237X111-3N
R5, R23, R27, R30, R37: 10k; RESC2012X65
R6, R24: 4.7k; RESC2012X65
R38, R39: 1k; RESC2012X65
SH4: SHORT-HT5; SHORT_TOP-50
U3: RFM98W-433S2; XCVR_RFM98W-433S2
Z1, Z2: MM3Z3V0ST1G; SOD2512X110N

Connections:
3.3V1: C14.1, IC5.8 (VCC), Q13.1 (G), R27.2, U3.13 (3.3V); also elsewhere on the board
5V1: C9.1, C13.1, D4.1 (K), D9.1 (K), IC1.P$5 (VDD), IC2.P$5 (VDD), LED5.VDD, LED6.VDD, LS1.P, LS2.P, R30.2; also elsewhere on the board
A10: R5.1, R6.2, Z1.1 (K); also elsewhere on the board
A11: R23.1, R24.2, Z2.1 (K); also elsewhere on the board
BAT1_OUT: R5.2; also elsewhere on the board
BAT2_OUT: R37.2; also elsewhere on the board
BUZZER_A: R39.2; also elsewhere on the board
BUZZER_T: R38.2; also elsewhere on the board
CS_FLASH: IC5.1 (!CS); also elsewhere on the board
CS_MPU1: IC1.P$4 (CS_MPU); also elsewhere on the board
CS_MPU2: IC2.P$4 (CS_MPU); also elsewhere on the board
CS_MS1: IC1.P$1 (CS_MS); also elsewhere on the board
CS_MS2: IC2.P$1 (CS_MS); also elsewhere on the board
GND: C9.2, C13.2, C14.2, IC1.P$6 (GND), IC2.P$6 (GND), IC5.4 (GND), LED5.VSS (GND), LED6.VSS (GND), Q14.2 (E), Q15.2 (E), R6.1, R24.1, SH4.2, Z1.2 (A), Z2.2 (A); also elsewhere on the board
HOLD: IC5.7 (!HOLD(IO3)); also elsewhere on the board
LED_CTRL: Q13.3 (S), R27.1; also elsewhere on the board
LORA_GND: ANT.2, ANT.3, ANT.4, ANT.5, SH4.1, U3.1 (GND), U3.8 (GND), U3.10 (GND)
MISO0: IC1.P$2 (SD0/MISO), IC2.P$2 (SD0/MISO); also elsewhere on the board
MISO1: IC5.2 (DO(IO1)), U3.2 (MISO); also elsewhere on the board
MOSI0: IC1.P$8 (MOSI/SDA), IC2.P$8 (MOSI/SDA); also elsewhere on the board
MOSI1: IC5.5 (DI(IO0)), U3.3 (MOSI); also elsewhere on the board
MPU1_INT: IC1.P$3 (INT); also elsewhere on the board
MPU_INT2: IC2.P$3 (INT); also elsewhere on the board
unnamed: LED5.DOUT (DO), LED6.DIN (DI)
unnamed: LED5.DIN (DI), Q13.2 (D), R30.1
unnamed: R23.2, R37.1
unnamed: D4.2 (A), LS2.N, Q14.3 (C)
unnamed: Q14.1 (B), R38.1
unnamed: D9.2 (A), LS1.N, Q15.3 (C)
unnamed: Q15.1 (B), R39.1
RFM_ANT: ANT.1, U3.9 (ANT)
RFM_INT: U3.14 (DIO0); also elsewhere on the board
RFM_NSS: U3.5 (NSS); also elsewhere on the board
RFM_RST: U3.6 (RESET); also elsewhere on the board
SCK0: IC1.P$7 (SCK/SCL), IC2.P$7 (SCK/SCL); also elsewhere on the board
SCK1: IC5.6 (CLK), U3.4 (SCK); also elsewhere on the board
WP: IC5.3 (!WP(IO2)); also elsewhere on the board

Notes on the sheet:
Flash memory
LoRa transceiver
10 dof breakouts
Battery voltage reading
Status LED
Buzzers

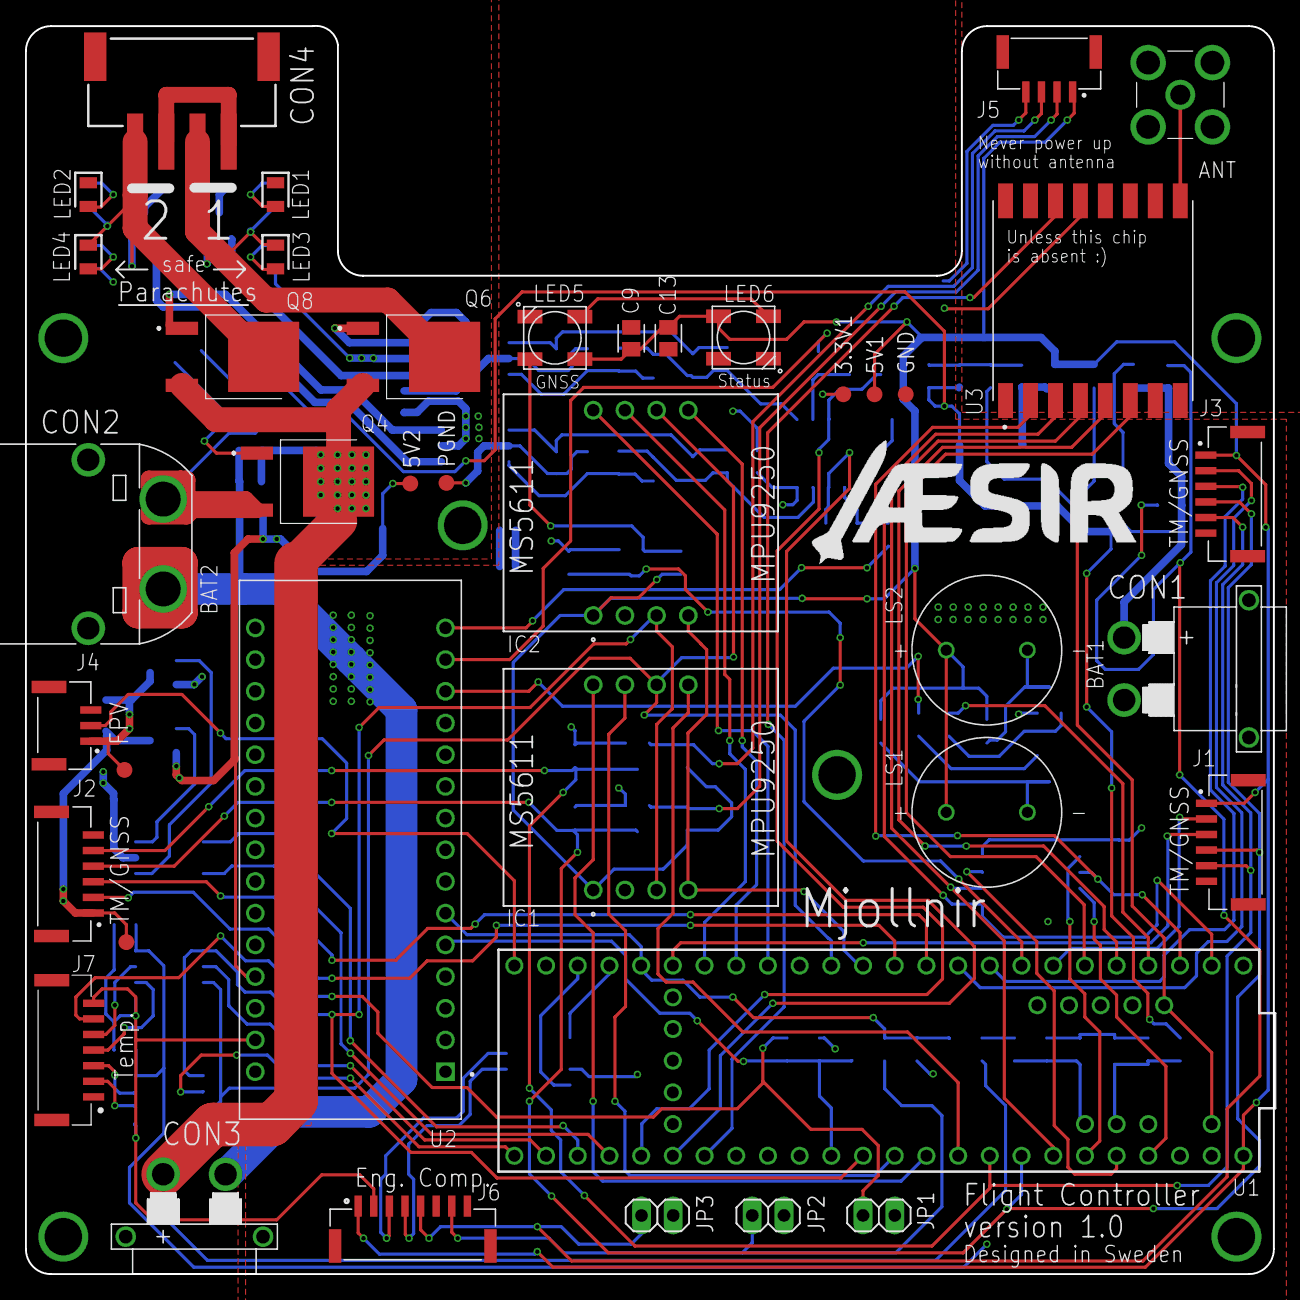
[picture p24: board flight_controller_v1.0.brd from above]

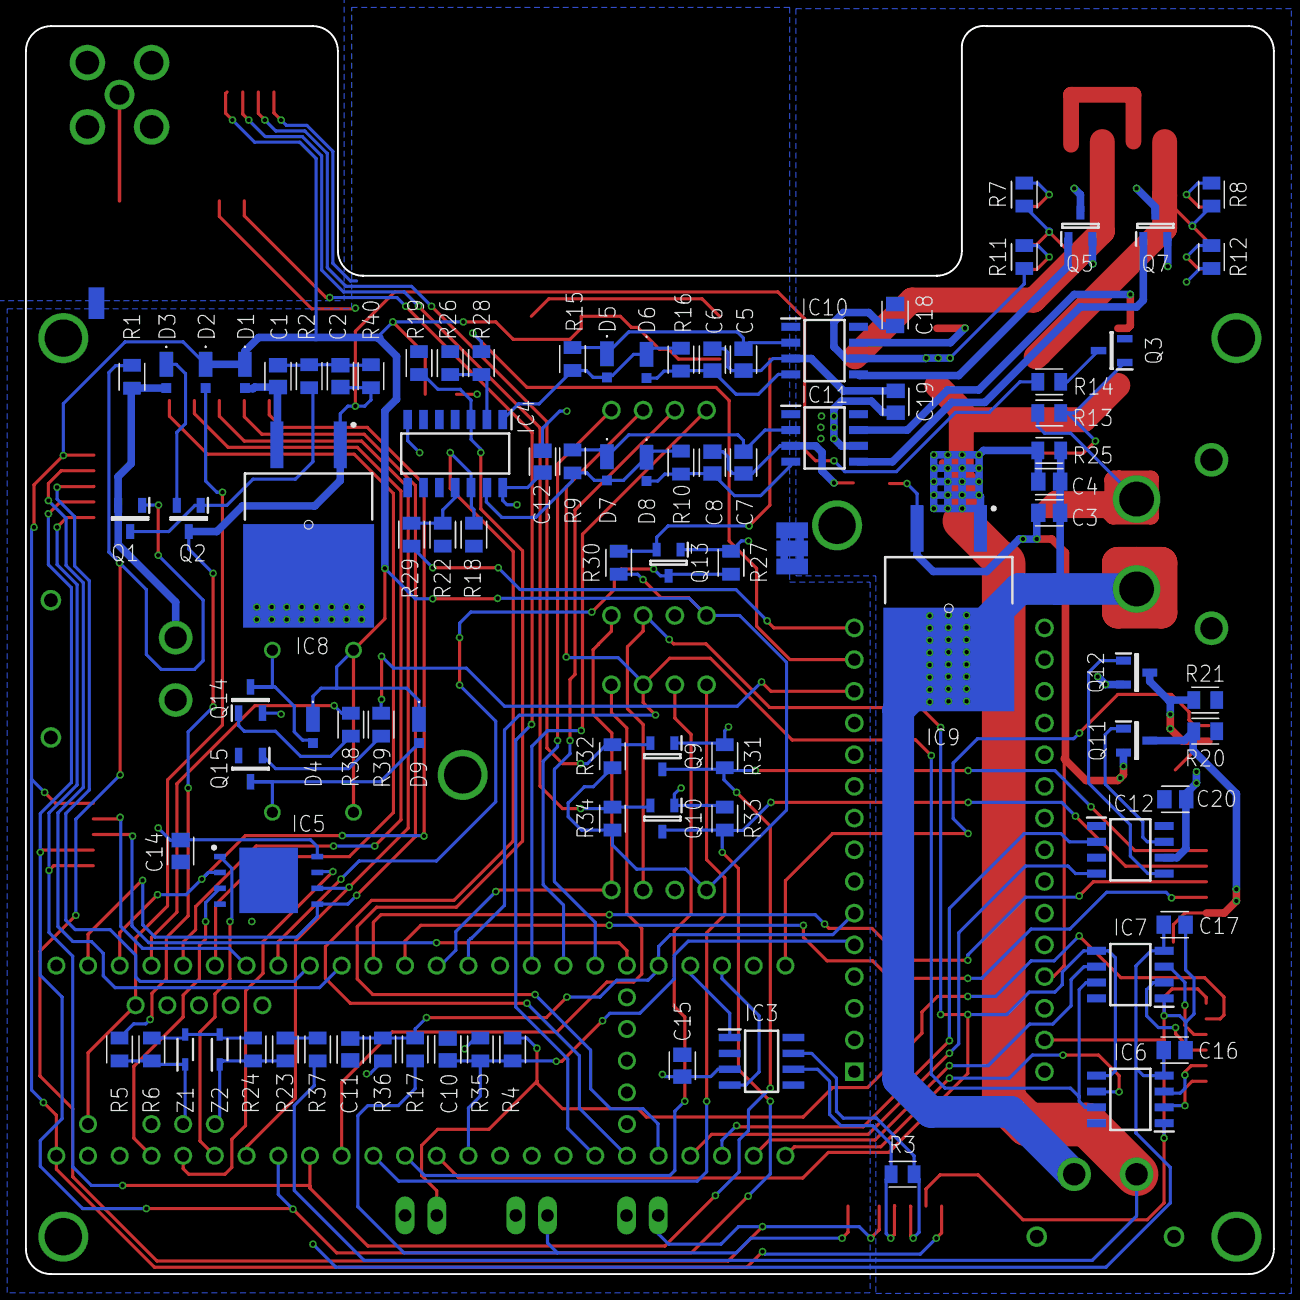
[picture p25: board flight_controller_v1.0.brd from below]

Board: 4 copper layers, 100.0 x 100.0 mm, 135 parts (95 on the bottom side), 102 nets.

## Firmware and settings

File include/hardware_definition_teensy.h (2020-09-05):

/* Pin definition for the Teensy */
#define PIN_MOSI1 0
#define PIN_MISO1 1
#define PIN_BUZZER 2
#define PIN_RFM_NSS 3
#define PIN_RFM_RST 4
#define PIN_TX1 5
#define PIN_LED_CTRL 6
#define PIN_RX3 7
#define PIN_TX3 8
#define PIN_RX2 9
#define PIN_TX2 10
#define PIN_MOSI0 11
#define PIN_MISO0 12
#define PIN_LIFTOFF1 13
#define PIN_SCK0 14
#define PIN_MPU1_INT 15
#define PIN_CS_MPU1 16
#define PIN_CS_MS1 17
#define PIN_SDA0 18
#define PIN_SCL0 19
#define PIN_SCK1 20
#define PIN_CS_FLASH 21
#define PIN_HOLD 22
#define PIN_WP 23
#define PIN_CS_MPU2 24
#define PIN_CS_MS2 25
#define PIN_MPU_INT2 26
#define PIN_RX1 27
#define PIN_LIFTOFF2 28
#define PIN_CAN0_TX 29
#define PIN_CAN0_RX 30
#define PIN_RX4 31
#define PIN_TX4 32
#define PIN_CS_TEMP1 33
#define PIN_CS_TEMP2 34
#define PIN_J2_DIS 35
#define PIN_J4_DIS 36
#define PIN_PARA1 37
#define PIN_PARA2 38
#define PIN_RFM_INT 39
#define PIN_BAT1 A10
#define PIN_BAT2 A11

/* Port definition for the Teensy */
#define PORT_MPU1 SPI
#define PORT_MPU2 SPI
#define PORT_MS1 SPI
#define PORT_MS2 SPI
#define PORT_RFM SPI1

/* Other definitions */
#define NUM_RGB_LEDS 2
#define BUZZER_FREQ 2400  // Hz

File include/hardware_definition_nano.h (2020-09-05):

/* Pin definition for the Teensy */
#define PIN_LIFTOFF1 2
#define PIN_LIFTOFF2 3
#define PIN_BUZZER 10
#define PIN_PARA1 11
#define PIN_PARA2 12

/* Other definitions */
#define BUZZER_FREQ 2400  // Hz

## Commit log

2020-08-03 doc: microcontrollers and battery inputs
2020-08-15 leave frame IDs non allocated for future use
2020-08-16 add placeholder for time sync frame
2020-09-05 replace 'sleep mode' with 'power mode'
2020-09-05 add unit tests for arduino nano
2020-09-05 doc: describe power setup
2020-09-05 doc: add board capabilities overview
2020-09-05 doc: add connectors
2020-09-05 doc: a word on parachute drivers
2020-09-05 add eagle source files
    [flight_controller_v1.0.brd, flight_controller_v1.0.sch]

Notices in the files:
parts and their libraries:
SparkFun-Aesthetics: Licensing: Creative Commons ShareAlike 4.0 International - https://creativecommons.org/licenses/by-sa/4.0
